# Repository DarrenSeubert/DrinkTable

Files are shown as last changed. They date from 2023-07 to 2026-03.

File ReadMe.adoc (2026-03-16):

= Drink Table  

An Amazon Alexa-enabled IoT device that mixes and pours drinks.  

Alexa treats this table as a dimmable light. A given brightness percentage represents a drink 
selection or a command for the table to execute.  

https://github.com/user-attachments/assets/83653fed-f806-43cc-ba11-e9e344582d79  

== Step 1: Installation  

1. Download this repository.  
2. Create an Arduino IoT Cloud Thing.  
3. Create a cloud variable named `drinkSelection` and configure it as follows:  
   - Type: Dimmed Light  
   - Permissions: Read & Write  
   - Trigger: On Change  
4. Set up the associated device as an ESP32 and configure it with your Wi-Fi username and password.  
5. Copy the contents of `DrinkTable.ino` into your main Arduino file.  
6. Install the required libraries and resolve any variable name conflicts.  

== Step 2: Assemble the Circuit  

Assemble the circuit following the diagram in `ESP32Wiring.pdf`.  

== Step 3: Load the Code  

1. Upload the code from this sketch onto an ESP32 board.  
2. In the Alexa app:  
   - Add the Arduino IoT skill.  
   - Link your account.  
3. Have Alexa search for new devices and add the table controller.  
4. Set up routines to define what phrases correspond to specific drinks or actions.  

=== Folder Structure  

....  
DrinkTable                => Arduino sketch folder  
├── CADFiles             => Folder with all 3D printed parts  
├── DrinkTable.ino       => Main Arduino file  
├── ESP32Wiring.pdf      => Circuit wiring diagram for the ESP32 board  
├── Guide.pdf            => Usage guide and blink code reference  
├── ReadMe.adoc          => This file  
├── sketch.json          => Sketch metadata file  
└── thingProperties.h    => Header file for the IoT device  
....  

=== Bill of Materials (BOM)  

For a rough BOM for this project, refer to this https://docs.google.com/spreadsheets/d/1IcMglOSQPUuBVhDI59dvtKw1fak_Vcd6wv3FlI9-fAY/edit?usp=sharing[BOM link].  

For the CAD files and 3D-printed parts used in this project, refer to the 
https://github.com/DarrenSeubert/DrinkTable/tree/main/CADFiles[CADFiles] folder.  

=== External Resources  

Here are some resources that were helpful during this project:  

- https://lastminuteengineers.com/esp32-pinout-reference/[ESP32 Pinout Reference]  
- https://randomnerdtutorials.com/esp32-i2c-communication-arduino-ide/#:~:text=When%20using%20the%20ESP32%20with,to%20use%20any%20other%20pins[ESP32 I2C Communication]
- https://learn.sparkfun.com/tutorials/apds-9960-rgb-and-gesture-sensor-hookup-guide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[APDS-9960 Sensor Guide]
- https://docs.arduino.cc/arduino-cloud/getting-started/cloud-variables[Arduino IoT Cloud Variables]
- https://blog.arduino.cc/2019/11/12/create-a-voice-controlled-device-with-alexa-and-arduino-iot-cloud-in-7-minutes/[Alexa and Arduino IoT Cloud Integration]  

Videos:  

- https://www.youtube.com/watch?v=F9UASFoUwiQ[Can Alexa/Siri Be Your Bartender?]
- https://www.youtube.com/watch?v=nR24z26chBI[I Need To Stop Making Smart Furniture]  

=== Disclaimers  
- DO NOT keep liquids that need to be refrigerated or closed inside of the table after opening for 
an extended period of time. This could lead to bacteria and mold growth.
- The current setup tends to leave a plastic-like taste in the liquids poured. I was unable to 
identify a root cause for this issue, and I am uncertain about how serious the concern may be.

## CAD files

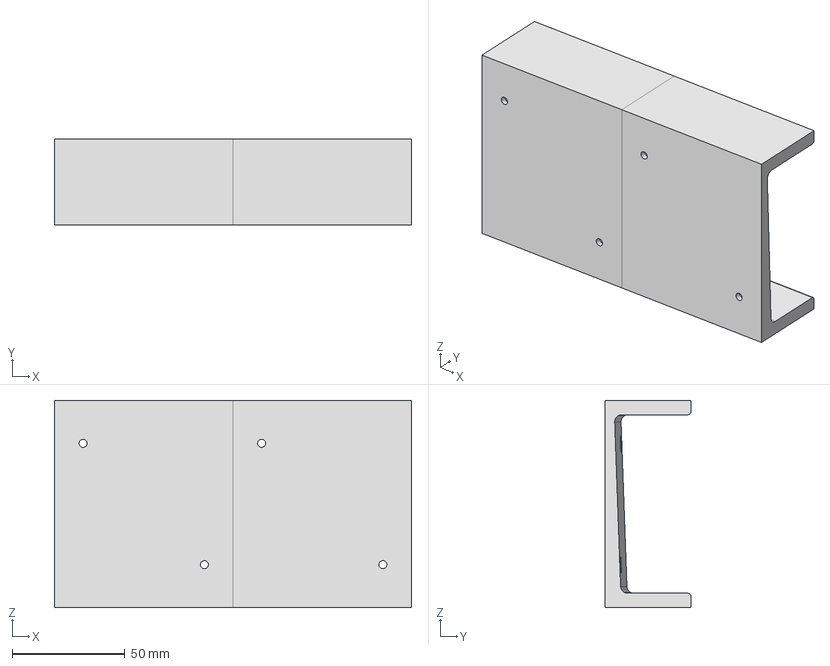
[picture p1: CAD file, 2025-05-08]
CADFiles/BottleHolderDoubleV1Assembly.stp
158.5 x 38.1 x 91.9 mm
BottleHolderV4 x 2

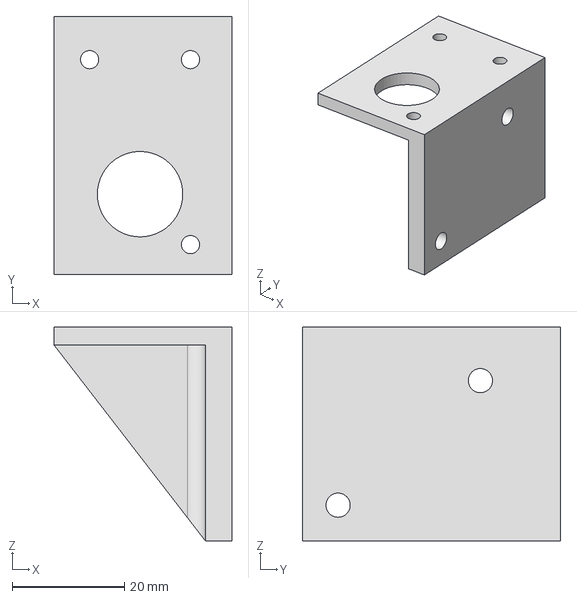
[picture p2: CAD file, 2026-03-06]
CADFiles/MotorMountV1.stp
31.8 x 46.0 x 38.1 mm

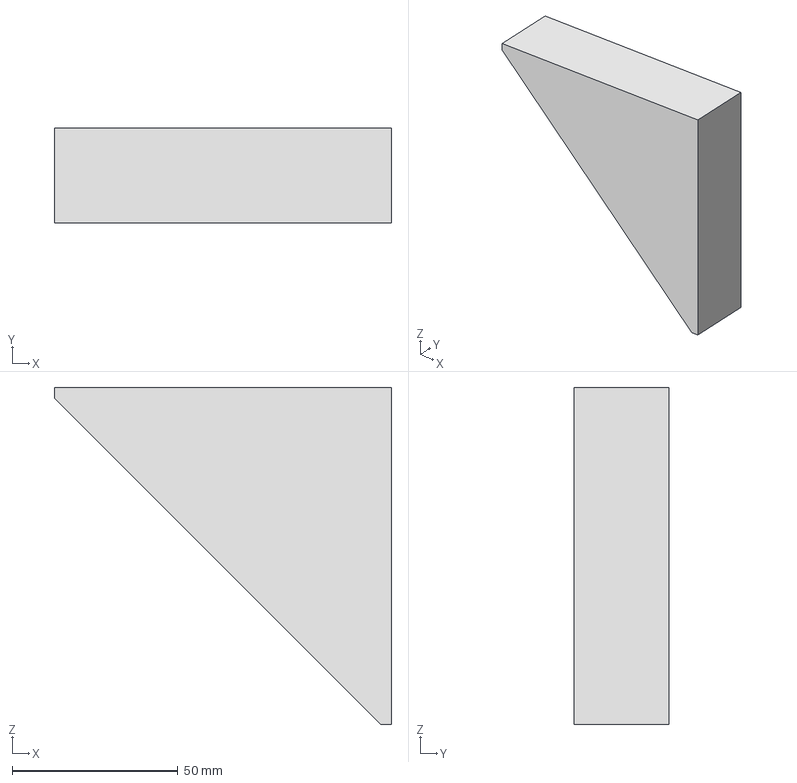
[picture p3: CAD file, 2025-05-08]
CADFiles/PrototypesMocksAndJigs/RightAngleJigV1.stp
101.6 x 28.6 x 101.6 mm

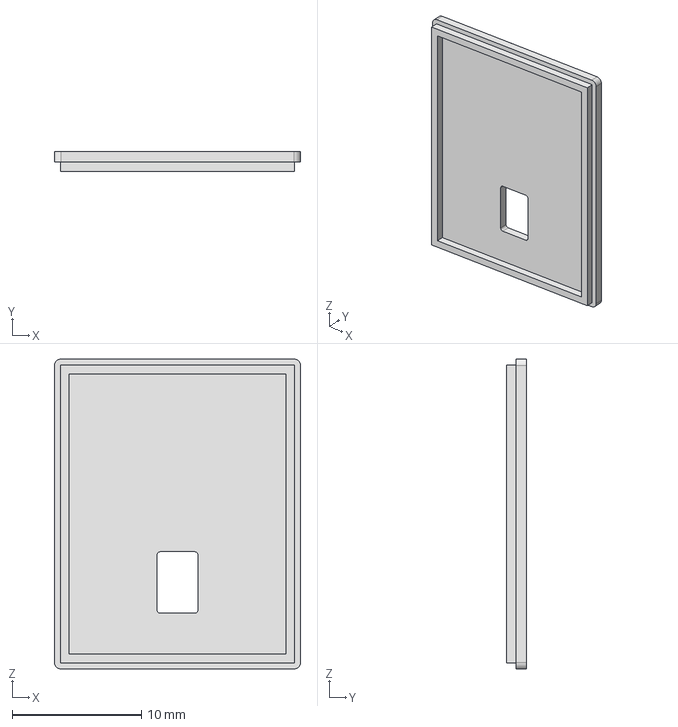
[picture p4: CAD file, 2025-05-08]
CADFiles/PrototypesMocksAndJigs/ProximitySensorCoverV1.stp
19.0 x 1.53 x 24.0 mm

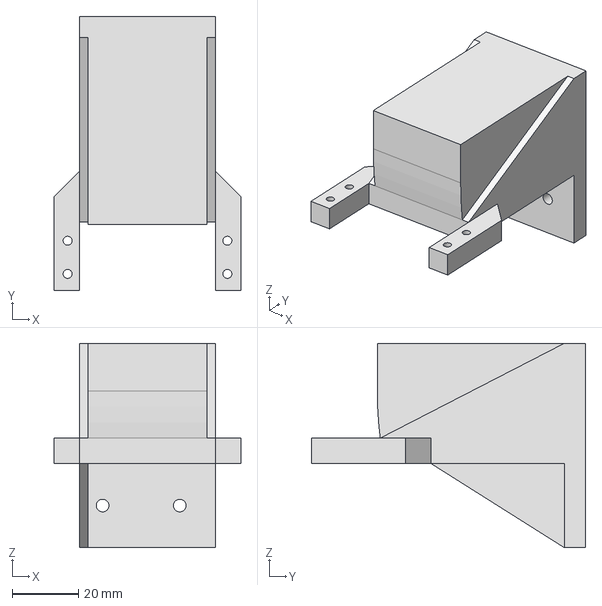
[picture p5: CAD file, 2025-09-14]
CADFiles/ServoMountV1.stp
56.3 x 82.6 x 61.6 mm

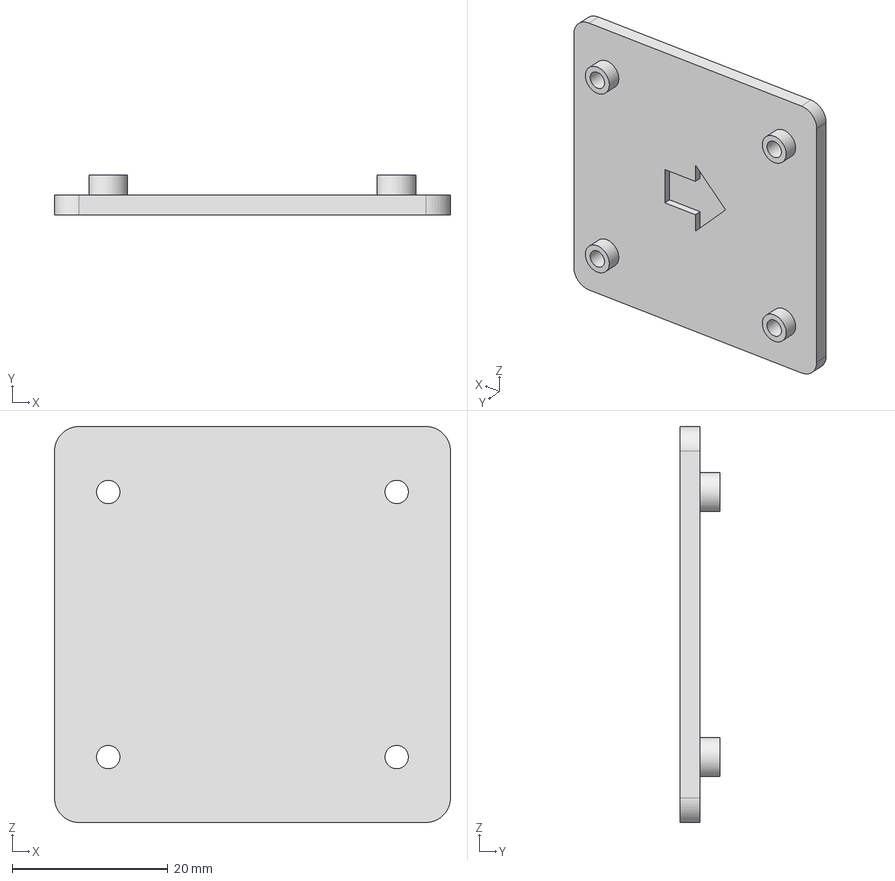
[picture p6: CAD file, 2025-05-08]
CADFiles/PrototypesMocksAndJigs/PumpJigV1.stp
50.8 x 5.08 x 50.8 mm

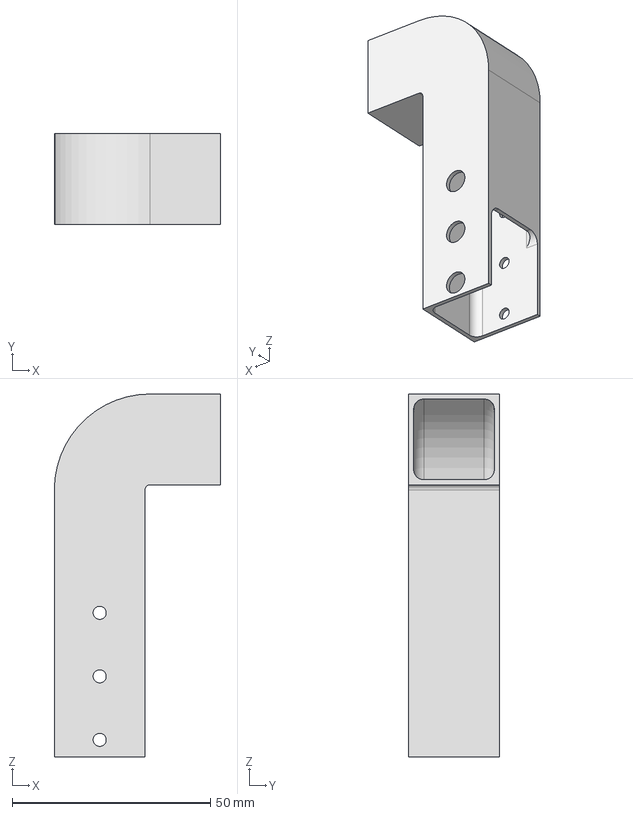
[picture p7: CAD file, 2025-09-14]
CADFiles/ServoHornV1.stp
41.9 x 22.9 x 91.4 mm

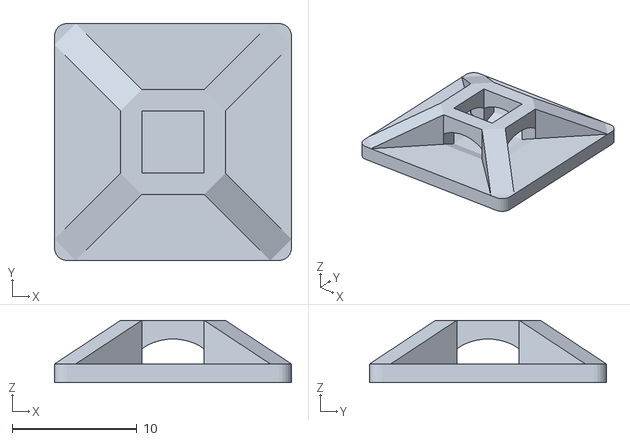
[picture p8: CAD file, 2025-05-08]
CADFiles/CableTieBaseV1.stl
19.0 x 19.0 x 5.01

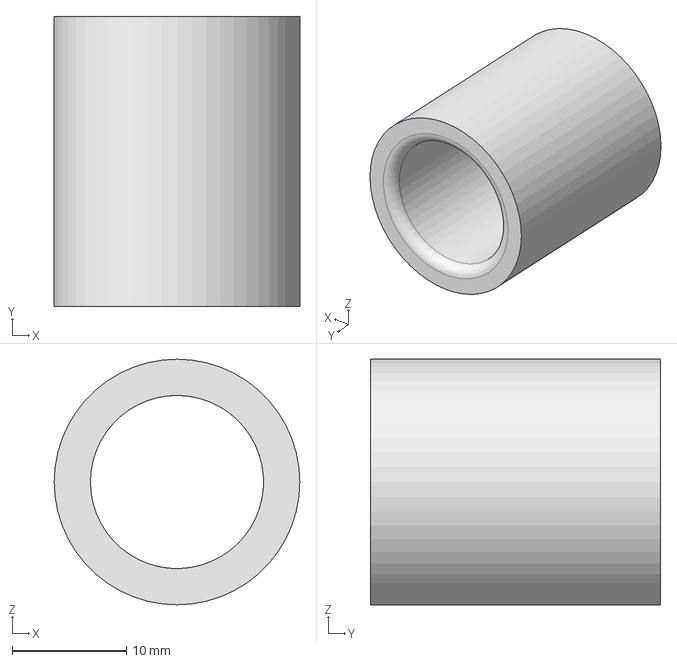
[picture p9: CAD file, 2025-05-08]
CADFiles/PrototypesMocksAndJigs/BearingTestFitV1.stp
21.5 x 25.4 x 21.5 mm

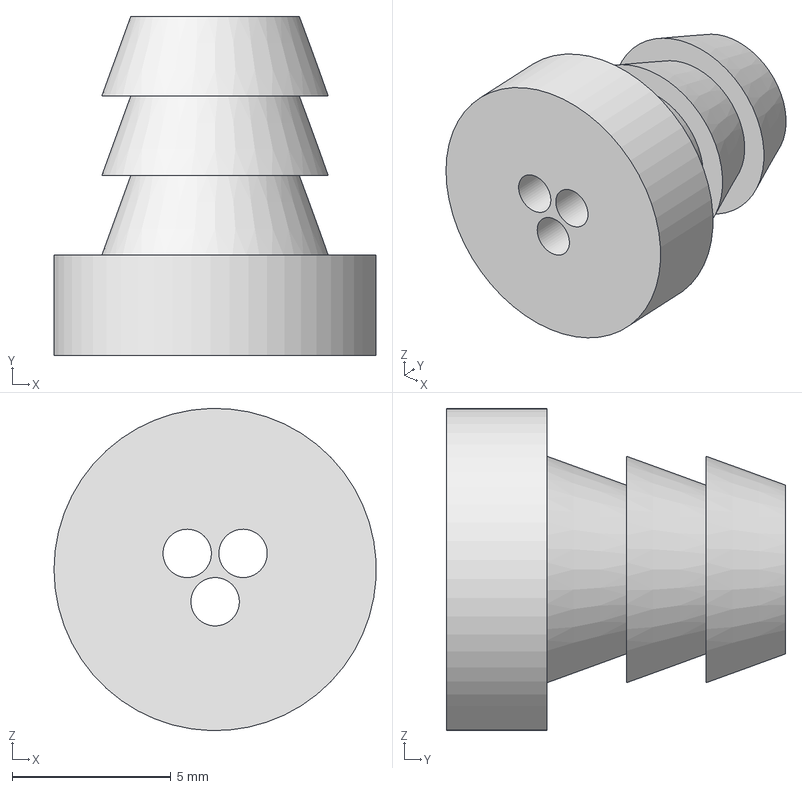
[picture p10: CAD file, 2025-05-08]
CADFiles/PrototypesMocksAndJigs/HoseBarbV1.stp
10.2 x 10.7 x 10.2 mm

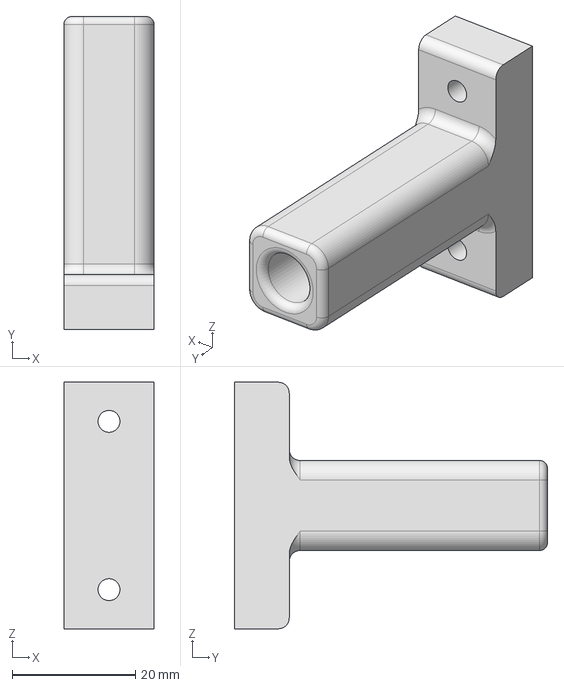
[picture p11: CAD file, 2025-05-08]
CADFiles/RodHolderBottomV1.stp
14.6 x 50.8 x 40.0 mm

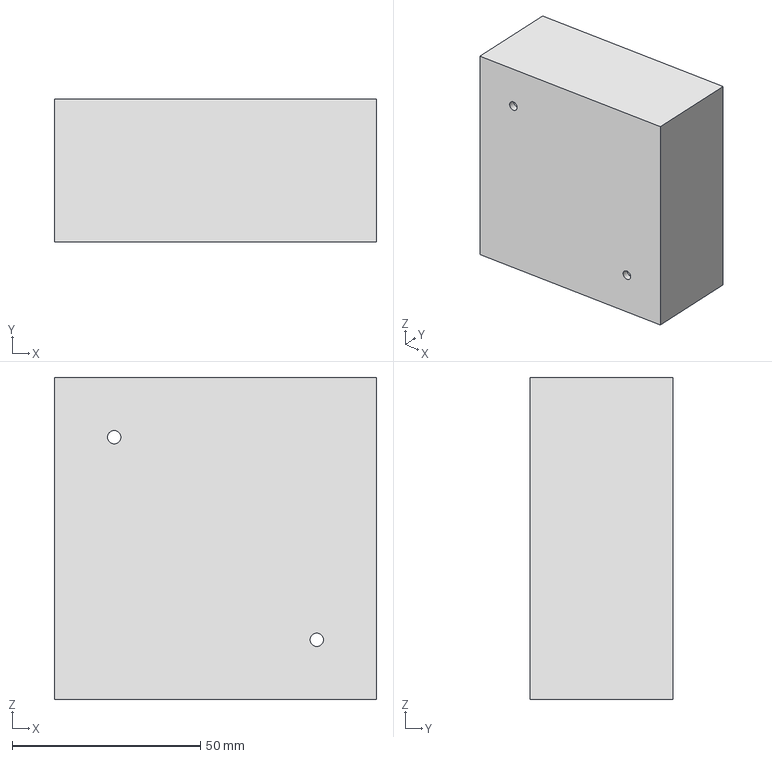
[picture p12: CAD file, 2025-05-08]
CADFiles/BottleHolderSingleV1.stp
85.6 x 38.1 x 85.6 mm

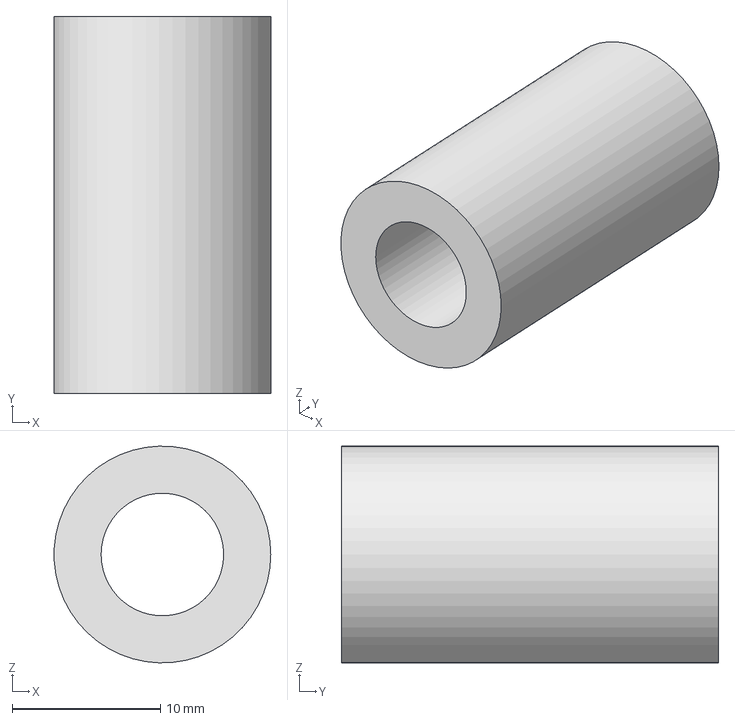
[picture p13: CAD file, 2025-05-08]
CADFiles/PrototypesMocksAndJigs/RodTestFitV1.stp
14.6 x 25.4 x 14.6 mm

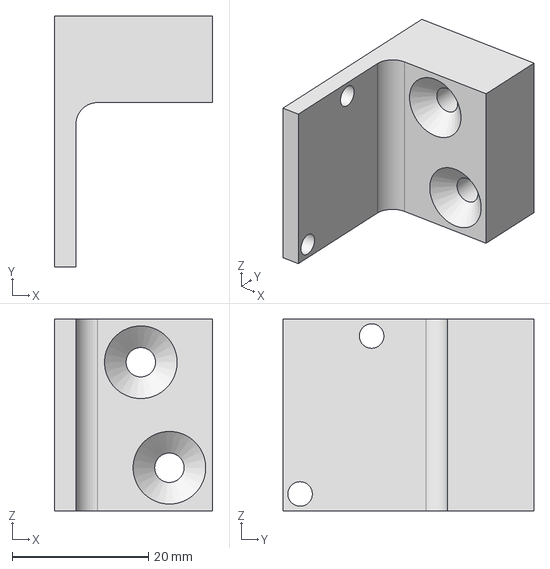
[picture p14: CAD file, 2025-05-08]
CADFiles/LimitSwitchTopV1.stp
23.2 x 36.8 x 28.2 mm

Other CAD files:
CADFiles/PrototypesMocksAndJigs/ProximitySensorBoxV1.stp
CADFiles/BevelV1.stp
CADFiles/PrototypesMocksAndJigs/TableMockUpV1.stp
CADFiles/LimitSwitchBottomV1.stp
CADFiles/BevelV1.ipt
CADFiles/BevelV1.stl
CADFiles/BottleHolderDoubleV1.ipt
CADFiles/BottleHolderDoubleV1.stp
CADFiles/BottleHolderDoubleV1Assembly.iam
CADFiles/BottleHolderDoubleV1Assembly.stl
CADFiles/BottleHolderSingleV1.ipt
CADFiles/BottleHolderSingleV1.stl
CADFiles/CarriageV1.ipt
CADFiles/CarriageV1.stl
CADFiles/CarriageV1.stp
CADFiles/LimitSwitchBottomV1.ipt
CADFiles/LimitSwitchBottomV1.stl
CADFiles/LimitSwitchTopV1.ipt
CADFiles/LimitSwitchTopV1.stl
CADFiles/MotorMountV1.ipt
CADFiles/MotorMountV1.stl
CADFiles/PrototypesMocksAndJigs/BearingTestFitV1.ipt
CADFiles/PrototypesMocksAndJigs/BearingTestFitV1.stl
CADFiles/PrototypesMocksAndJigs/HoseBarbV1.ipt
CADFiles/PrototypesMocksAndJigs/HoseBarbV1.stl
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

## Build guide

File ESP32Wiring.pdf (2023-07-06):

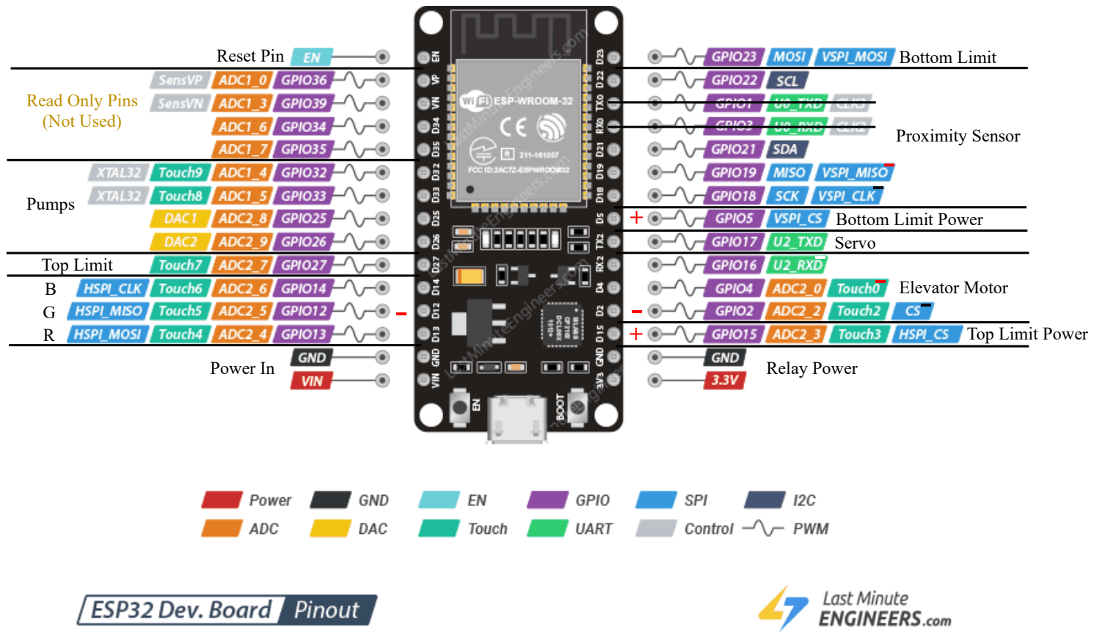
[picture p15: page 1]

RGB

Top Limit

Pumps

Power In

Read Only Pins
(Not Used)

Bottom Limit

Proximity Sensor

-⁺+ | Top Limit Power

Elevator Motor

Servo

Bottom Limit Power

Reset Pin

Relay Power

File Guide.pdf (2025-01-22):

How to Use the Drink Table
- Alexa, what drinks are available?
- Set a glass on the center of platform.
- Alexa, can I get a *size of drink* *name of drink*.
- Wait for your drink to be prepared.

Drink Table Blink Codes
- White:
1) Error Successfully Cleared
2) Glass is not Present
3) Invalid Drink Selection
4) Recent Pour, Replace Glass with a New One
- Red:
2) Elevator Movement Timed Out
3) Pumping Liquid Failed
- Blue:
Flashing) Connecting to the Internet
- Green:
1) Connected to the Internet and Ready

Drink Table Admin Controls
- Alexa, Drink Table clear error.
- Alexa, Drink Table home top.
- Alexa, Drink Table home bottom.

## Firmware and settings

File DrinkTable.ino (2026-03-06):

#include "arduino_secrets.h"
#include "thingProperties.h"

#include <ESP32Servo.h> // ESP32Servo - Version: Latest
#include <SparkFun_APDS9960.h> // SparkFun APDS9960 RGB and Gesture Sensor - Version: Latest
#include <Wire.h> // For IC2 Communication

// Declarations
enum RGBColor {
  Red, Green, Blue, Yellow, Cyan, Purple, White, Black
};

const int red = 13;
const int green = 12;
const int blue = 14;

const int pump1 = 26; // Apple Brandy
const int pump2 = 25; // Punch
const int pump3 = 33; // UV Blue
const int pump4 = 32; // Lemonade

Servo servo;
const int servoPin = 17;

const int elevatorMotorPin1 = 4;
const int elevatorMotorPin2 = 2;
const int elevatorMotorPWM = 16;
const int elevatorMotorChannel = 2;
const int elevatorMotorFrequency = 5000;
const int elevatorMotorResolution = 8;

const int topLimit = 27;
const int topLimitPower = 15;
const int bottomLimit = 23;
const int bottomLimitPower = 5;

SparkFun_APDS9960 prox = SparkFun_APDS9960();
const int proxPower = 19;
const int proxGround = 18;

boolean firstRun = true;

boolean errorState = false;
int errorBlinkCode = 0;

boolean recentPour = false;

const double shotPumpTime = 6.0;
const double mixerPumpTime = 8.5;

/// @brief Function called once on boot of program
void setup() {
  pinMode(red, OUTPUT);
  pinMode(green, OUTPUT);
  pinMode(blue, OUTPUT);

  pinMode(pump1, OUTPUT);
  pinMode(pump2, OUTPUT);
  pinMode(pump3, OUTPUT);
  pinMode(pump4, OUTPUT);
  digitalWrite(pump1, LOW);
  digitalWrite(pump2, LOW);
  digitalWrite(pump3, LOW);
  digitalWrite(pump4, LOW);

  pinMode(elevatorMotorPin1, OUTPUT);
  pinMode(elevatorMotorPin2, OUTPUT);

  pinMode(topLimit, INPUT_PULLDOWN);
  pinMode(topLimitPower, OUTPUT);
  pinMode(bottomLimit, INPUT_PULLDOWN);
  pinMode(bottomLimitPower, OUTPUT);

  pinMode(proxPower, OUTPUT);
  pinMode(proxGround, OUTPUT);

  Serial.begin(9600); // Initialize serial and wait for port to open:
  delay(1500); // Delay briefly to allow a Serial Monitor to connect without blocking if none found
  initProperties(); // Defined in thingProperties.h
  ArduinoCloud.begin(ArduinoIoTPreferredConnection); // Connect to Arduino IoT Cloud

  // Gets network/IoT Cloud connection status and errors (0 = errors only, 4 = maximum detail).
  setDebugMessageLevel(2);
  ArduinoCloud.printDebugInfo();

  servo.attach(servoPin);
  servoSetPosition(0.0);
  
  ledcSetup(elevatorMotorChannel, elevatorMotorFrequency, elevatorMotorResolution);
  ledcAttachPin(elevatorMotorPWM, elevatorMotorChannel);
  digitalWrite(elevatorMotorPin1, HIGH);
  digitalWrite(elevatorMotorPin2, HIGH);
  ledcWrite(elevatorMotorChannel, 0);
  
  digitalWrite(topLimitPower, HIGH);
  digitalWrite(bottomLimitPower, HIGH);
  
  digitalWrite(proxPower, HIGH);
  digitalWrite(proxGround, LOW);
  delay(500); // Delay for proximity sensor to power on

  prox.init(); // Initialize APDS-9960 (configure I2C and initial values)
  prox.setProximityGain(0); // Adjust the Proximity sensor gain. 0: 1x, 1: 2x, 2: 4x, 3: 8x
  prox.enableProximitySensor(false); // Start running the prox-9960 proximity sensor (no interrupts)
}

/// @brief Function called repeatedly during execution of program
void loop() {
  // Check if connected to Arduino IoT Cloud
  if (!ArduinoCloud.connected()) {
    Serial.println("Connecting to Arduino IoT Cloud...");
    firstRun = true;
    connectionBlink(false);
  }

  // Check that resets recentPour
  if (recentPour && !isGlassPresent()) {
    recentPour = false;
  }

  ArduinoCloud.update();
}

/// @brief Function called when a change in Drink Selection is detected
void onDrinkSelectionChange()  {
  // Check if the change is due to connecting to the internet
  if (firstRun) {
    firstRun = false;
    connectionBlink(true);
    return;
  }
  
  // Retrieve the table code and reset it back to 0
  int tableCode = drinkSelection.getBrightness();
  drinkSelection.setBrightness(0);
  Serial.println("-------");
  Serial.print("Table Code: ");
  Serial.println(tableCode);

  // Clear Error State of Table
  if (tableCode == 99) {
    errorState = false;
    errorBlinkCode = 0;
    Serial.println("Error State Cleared");
    errorBlink(1, false);
    return;
  }

  // Checks if Table is in Error State
  if (errorState) {
    Serial.println("Error: Table in Error State, Please Correct and Clear the Error");
    errorBlink(errorBlinkCode, true);
    return;
  }

  // Homes Table to Top Limit
  if (tableCode == 97) {
    Serial.println("Homing to Top Limit...");
    if (!elevatorMove(true)) { // Move Up until Top Limit
      Serial.println("Error: Elevator Movement Timed Out");
      errorBlink(2, true);
    }

    return;
  }

  // Homes Table to Bottom Limit
  if (tableCode == 98) {
    Serial.println("Homing to Bottom Limit...");
    if (!elevatorMove(false)) { // Move Up until Top Limit
      Serial.println("Error: Elevator Movement Timed Out");
      errorBlink(2, true);
    }

    return;
  }

  // Checks if the Glass has been Replaced
  if (recentPour) {
    Serial.println("Error: Table has Detected a Recent Pour, Replace the Glass with a New One");
    errorBlink(4, false);
    return;
  }

  // Checks if a Glass is Present
  if (!isGlassPresent()) {
    Serial.println("Error: Glass is not Present");
    errorBlink(2, false);
    return;
  }

  // Detects a Non-Valid Drink is Selected
  double pump1Time = 0.0, pump2Time = 0.0, pump3Time = 0.0, pump4Time = 0.0;
  if (!getPumpTimes(tableCode, pump1Time, pump2Time, pump3Time, pump4Time)) {
    Serial.println("Error: Invalid Drink Selection");
    errorBlink(3, false);
    return;
  }
  Serial.println("-Pump Times-");
  Serial.println(pump1Time);
  Serial.println(pump2Time);
  Serial.println(pump3Time);
  Serial.println(pump4Time);

  // Drink Routine Starts Here
  if (!elevatorMove(false)) { // Move Elevator Down until Bottom Limit
    Serial.println("Error: Elevator Movement Timed Out");
    errorBlink(2, true);
    return;
  }

  // Move Servo to Pouring Position
  servoSetPosition(1.0);
  delay(500);

  // Pump Liquid
  if (!pumpLiquid(pump1Time, pump2Time, pump3Time, pump4Time)) {
    Serial.println("Error: Pump Liquid Failed");
    servoSetPosition(0.0);
    errorBlink(3, true);
    return;
  }
  delay(1500);
  
  // Move Servo to Stored Position
  servoSetPosition(0.0);
  delay(500);

  // Move Elevator Up until Top Limit
  if (!elevatorMove(true)) {
    Serial.println("Error: Elevator Movement Timed Out");
    errorBlink(2, true);
    return;
  }

  setColor(Black);
}

/// @brief Function that determines if a glass is present
/// @return True if a glass is present, false if not present or if there is an error reading the
/// value
boolean isGlassPresent() {
  uint8_t proxData;
  if (!prox.readProximity(proxData)) {
    Serial.println("Error: Could not Read Proximity Value");
    return false;
  } else {
    Serial.print("Proximity Value: ");
    Serial.println(proxData);
    return proxData > 230;
  }
}

/// @brief Function that sets the servo's position given a percent of rotation. To reduce noise from
/// constant minor corrections, the target position is adjusted by ±5 units after a short delay.
/// @param percent A value between 0.0 and 1.0 with 0.0 being stored position and 1.0 being pouring
/// position
void servoSetPosition(double percent) {
  if (percent < 0.0) {
    percent = 0.0;
  } else if (percent > 1.0) {
    percent = 1.0;
  }

  // Map the values 0.0-1.0 to 5-116
  int value = 111 * percent + 5;
  int prevValue = servo.read();
  servo.write(value);

  // Determine direction of travel
  if (abs(value - prevValue) > 5) {
    int adjustment = (value < prevValue) ? 5 : -5;
    
    // Let the servo move to the requested set position
    delay(1000);
    servo.write(value + adjustment);
  }
}

/// @brief Function that moves the elevator until the correct limit switch is pressed with a timeout
/// @param up Whether the desired movement of the elevator is up or down
/// @return True if the movement did not timeout, else false
boolean elevatorMove(boolean up) {
  unsigned long startTime = millis();
  const unsigned long timeout = 8000;

  // Select direction and limit switch depending on up
  double direction = up ? 1.0 : -1.0;
  int limitPin = up ? topLimit : bottomLimit;

  while (!digitalRead(limitPin) && (millis() - startTime) < timeout) {
    motorSetSpeed(elevatorMotorChannel, elevatorMotorPin1, elevatorMotorPin2, direction);
  }
  motorSetSpeed(elevatorMotorChannel, elevatorMotorPin1, elevatorMotorPin2, 0.0);

  return (millis() - startTime) < timeout;
}

/// @brief Function that sets a motor's speed and direction
/// @param motorChannel The channel that the motor controller is running on
/// @param pin1 One of the pins that the motor controller is plugged into
/// @param pin2 One of the pins that the motor controller is plugged into
/// @param percentage A value between -1.0 and 1.0 that represents the percentage and direction
/// for the motor to run
void motorSetSpeed(int motorChannel, int pin1, int pin2, double percentage) {
  if (percentage < -1.0) {
    percentage = -1.0;
  } else if (percentage > 1.0) {
    percentage = 1.0;
  }

  int value = round(abs(255 * percentage));
  if (percentage > 0.0) {
    digitalWrite(pin1, HIGH);
    digitalWrite(pin2, LOW);
    ledcWrite(motorChannel, value); 
  } else if (percentage < 0.0) {
    digitalWrite(pin1, LOW);
    digitalWrite(pin2, HIGH);
    ledcWrite(motorChannel, value);
  } else {
    digitalWrite(pin1, HIGH);
    digitalWrite(pin2, HIGH);
    ledcWrite(motorChannel, value);
  }
}

/// @brief Function that pumps liquid given the desired duration
/// @param pump1Time The desired pump time in seconds
/// @param pump2Time The desired pump time in seconds
/// @param pump3Time The desired pump time in seconds
/// @param pump4Time The desired pump time in seconds
/// @return True if the glass stays present for the duration of the function, else false
boolean pumpLiquid(double pump1Time, double pump2Time, double pump3Time, double pump4Time) {
  unsigned long pump1Dur = (unsigned long)(pump1Time * 1000.0);
  unsigned long pump2Dur = (unsigned long)(pump2Time * 1000.0);
  unsigned long pump3Dur = (unsigned long)(pump3Time * 1000.0);
  unsigned long pump4Dur = (unsigned long)(pump4Time * 1000.0);

  unsigned long maxPumpTime = max(max(pump1Dur, pump2Dur), max(pump3Dur, pump4Dur));
  unsigned long elapsedTime = 0;
  unsigned long startTime = millis();

  while (maxPumpTime > elapsedTime && isGlassPresent()) {
    elapsedTime = millis() - startTime;
    digitalWrite(pump1, elapsedTime < pump1Dur ? HIGH : LOW);
    digitalWrite(pump2, elapsedTime < pump2Dur ? HIGH : LOW);
    digitalWrite(pump3, elapsedTime < pump3Dur ? HIGH : LOW);
    digitalWrite(pump4, elapsedTime < pump4Dur ? HIGH : LOW);

    recentPour = true;
    delay(1);
  }

  digitalWrite(pump1, LOW);
  digitalWrite(pump2, LOW);
  digitalWrite(pump3, LOW);
  digitalWrite(pump4, LOW);

  return isGlassPresent();
}

/// @brief Function that sets the blink code and state of table and blinks LEDs
/// @param times Number of times for the LEDs to blink
/// @param state True if fatal error, false if warning error 
void errorBlink(int times, boolean state) {
  errorBlinkCode = times;
  errorState = state;
  RGBColor color;

  if (state) {
    color = Red;
  } else {
    color = White;
  }

  for (int i = 0; i < times; i++) {
    setColor(color);
    delay(250);
    setColor(Black);
    delay(250);
  }
}

/// @brief Function that blinks the LEDs to show the Arduino IoT Cloud connection state
/// @param connected True if the table is connected, false if not connected
void connectionBlink(boolean connected) {
  RGBColor color;
  int delayTime;
  
  if (connected) {
    color = Green;
    delayTime = 250;
  } else {
    color = Blue;
    delayTime = 1000;
  }
  
  setColor(color);
  delay(delayTime);
  setColor(Black);
  delay(delayTime);
}

/// @brief Function that sets the color of the LEDs
/// @param color The desired color for the LEDs to be set to
void setColor(RGBColor color) {
  switch (color) {
    case Red:
      digitalWrite(red, HIGH);
      digitalWrite(green, LOW);
      digitalWrite(blue, LOW);
      break;
    case Green:
      digitalWrite(red, LOW);
      digitalWrite(green, HIGH);
      digitalWrite(blue, LOW);
      break;
    case Blue:
      digitalWrite(red, LOW);
      digitalWrite(green, LOW);
      digitalWrite(blue, HIGH);
      break;
    case Yellow:
      digitalWrite(red, HIGH);
      digitalWrite(green, HIGH);
      digitalWrite(blue, LOW);
      break;
    case Cyan:
      digitalWrite(red, LOW);
      digitalWrite(green, HIGH);
      digitalWrite(blue, HIGH);
      break;
    case Purple:
      digitalWrite(red, HIGH);
      digitalWrite(green, LOW);
      digitalWrite(blue, HIGH);
      break;
    case White:
      digitalWrite(red, HIGH);
      digitalWrite(green, HIGH);
      digitalWrite(blue, HIGH);
      break;
    case Black:
      digitalWrite(red, LOW);
      digitalWrite(green, LOW);
      digitalWrite(blue, LOW);
      break;
    default:
      digitalWrite(red, LOW);
      digitalWrite(green, LOW);
      digitalWrite(blue, LOW);
      break;
  }
}

/// @brief Function that given the drink code will set the pump times and LED color
/// @param drinkCode The numeric code of the drink
/// @param pump1Time The run time to be set for pump1
/// @param pump2Time The run time to be set for pump2
/// @param pump3Time The run time to be set for pump3
/// @param pump4Time The run time to be set for pump4
/// @return True if a valid drink's pump times were calculated, else false 
boolean getPumpTimes(int drinkCode, double &pump1Time, double &pump2Time, double &pump3Time,
                     double &pump4Time) {
  boolean validDrink = false;

  switch (drinkCode) {
    case 1: // Apple Brandy Straight
      pump1Time = shotPumpTime; // Apple Brandy
      pump2Time = 0.0; // Punch
      pump3Time = 0.0; // UV Blue
      pump4Time = 0.0; // Lemonade
      setColor(Green);
      validDrink = true;
      break;
    case 2: // Large Apple Brandy Straight
      pump1Time = shotPumpTime * 2; // Apple Brandy
      pump2Time = 0.0; // Punch
      pump3Time = 0.0; // UV Blue
      pump4Time = 0.0; // Lemonade
      setColor(Green);
      validDrink = true;
      break;
    case 3: // UV Blue Straight
      pump1Time = 0.0; // Apple Brandy
      pump2Time = 0.0; // Punch
      pump3Time = shotPumpTime; // UV Blue
      pump4Time = 0.0; // Lemonade
      setColor(Blue);
      validDrink = true;
      break;
    case 4: // Large UV Blue Straight
      pump1Time = 0.0; // Apple Brandy
      pump2Time = 0.0; // Punch
      pump3Time = shotPumpTime * 2; // UV Blue
      pump4Time = 0.0; // Lemonade
      setColor(Blue);
      validDrink = true;
      break;
    case 5: // UV Blue Punch
      pump1Time = 0.0; // Apple Brandy
      pump2Time = mixerPumpTime; // Punch
      pump3Time = shotPumpTime; // UV Blue
      pump4Time = 0.0; // Lemonade
      setColor(Purple);
      validDrink = true;
      break;
    case 6: // Large UV Blue Punch
      pump1Time = 0.0; // Apple Brandy
      pump2Time = mixerPumpTime; // Punch
      pump3Time = shotPumpTime * 2; // UV Blue
      pump4Time = 0.0; // Lemonade
      setColor(Purple);
      validDrink = true;
      break;
    case 7: // UV Blue Lemonade
      pump1Time = 0.0; // Apple Brandy
      pump2Time = 0.0; // Punch
      pump3Time = shotPumpTime; // UV Blue
      pump4Time = mixerPumpTime; // Lemonade
      setColor(Cyan);
      validDrink = true;
      break;
    case 8: // Large UV Blue Lemonade
      pump1Time = 0.0; // Apple Brandy
      pump2Time = 0.0; // Punch
      pump3Time = shotPumpTime * 2; // UV Blue
      pump4Time = mixerPumpTime; // Lemonade
      setColor(Cyan);
      validDrink = true;
      break;
    case 9: // Punch
      pump1Time = 0.0; // Apple Brandy
      pump2Time = mixerPumpTime; // Punch
      pump3Time = 0.0; // UV Blue
      pump4Time = 0.0; // Lemonade
      setColor(Red);
      validDrink = true;
      break;
    case 10: // Large Punch
      pump1Time = 0.0; // Apple Brandy
      pump2Time = mixerPumpTime * 2; // Punch
      pump3Time = 0.0; // UV Blue
      pump4Time = 0.0; // Lemonade
      setColor(Red);
      validDrink = true;
      break;
    case 11: // Lemonade
      pump1Time = 0.0; // Apple Brandy
      pump2Time = 0.0; // Punch
      pump3Time = 0.0; // UV Blue
      pump4Time = mixerPumpTime; // Lemonade
      setColor(Yellow);
      validDrink = true;
      break;
    case 12: // Large Lemonade
      pump1Time = 0.0; // Apple Brandy
      pump2Time = 0.0; // Punch
      pump3Time = 0.0; // UV Blue
      pump4Time = mixerPumpTime * 2; // Lemonade
      setColor(Yellow);
      validDrink = true;
      break;
    default:
      pump1Time = 0.0; // Apple Brandy
      pump2Time = 0.0; // Punch
      pump3Time = 0.0; // UV Blue
      pump4Time = 0.0; // Lemonade
      setColor(Black);
      validDrink = false;
      break;
  }

  return validDrink;
}

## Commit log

2023-06-29 Fixed White RGB and elevator time
    [DrinkTable.ino]
2023-06-29 Updated Device Login Name
2023-06-29 Fixed pump time wrap and recentPour logic
    [DrinkTable.ino]
2023-06-29 Added ESP32 Wiring Diagram
2023-06-29 Flipped motor direction
2023-06-30 Updated Wiring Diagram
2023-06-30 Increased Elevator Timeout and change error type
    [DrinkTable.ino]
2023-07-05 Added Error State Clearing and Elevator Homing Controls
    [DrinkTable.ino]
2023-07-06 Update ESP32 Wiring.pdf
2023-07-06 Changed name of Wiring Diagram
2023-07-08 Updated print outs for debugging
2023-07-09 Removed proximity prints
2025-01-22 Added cheat sheet, comments, and fixed servo bug
    [DrinkTable.ino]
2025-04-10 Updated motorSetSpeed() logic
2025-05-08 Added CADFiles and updated ReadMe.adoc
    [BearingTestFitV1.ipt, BearingTestFitV1.stl, BearingTestFitV1.stp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]
2025-09-03 Moved servo attaching, cleanup
2025-09-05 Fixed elevator bug
    Hardcoded the elevator motor to PWM channel 2 to ensure no overlap with servo.
    Power and ground pins must be set first, then the speed pin.
    [DrinkTable.ino]
2025-09-14 Updated servo mount and horn
    [ServoHornV1.ipt, ServoHornV1.stl, ServoHornV1.stp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]
2025-09-16 Fixed servo noise issue
    Improved servoSetPosition to minimize noise by adding a small corrective adjustment after movement.
    [DrinkTable.ino]
2025-09-16 Tuned pump times, prox sensor, and servo
2025-09-17 Adjusted settle time for liquids being pumped
2025-09-18 Updated CAD folder name
    [BearingTestFitV1.ipt, BearingTestFitV1.stl, BearingTestFitV1.stp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]
2025-09-18 Fixed all wrap around logic, clean up
    [DrinkTable.ino]
2026-02-16 Tuned Servo
2026-02-26 Tuned servo range
2026-02-26 Changed pump2 liquid, fixed drink 8 pump times
    [DrinkTable.ino]
2026-03-06 Initialize variables, set pumps LOW on boot, add CPU delays
2026-03-06 Updated MotorMount to have larger big hole
    [MotorMountV1.ipt, MotorMountV1.stl, MotorMountV1.stp]
